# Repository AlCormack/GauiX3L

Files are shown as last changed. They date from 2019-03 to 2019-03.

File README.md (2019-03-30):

# Gaui X3L Speed
 
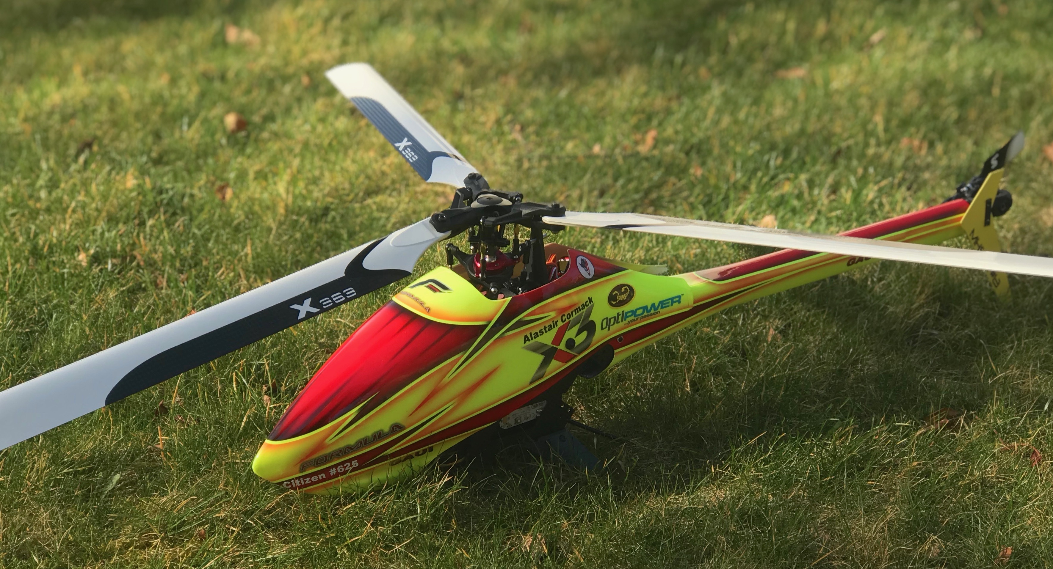
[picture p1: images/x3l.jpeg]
 <br />
 
A little video of it during a speed pass:<br />
 IMAGE ALT TEXT (http://www.youtube.com/watch?v=dyuTX_kXLzM "Gaui Speed X3L")
 
After getting my Gaui R5, I got the bug for speed. The R5 is a fantastic heli but I was looking for something even smaller for quick trips to the field. As it obviously had to be a Gaui heli the choice was simplified as the X3L had a fuselage and would support a motor that was much larger than a 325-380mm heli would normally use. The next decision was two or three blades. Never had a three blade heli and have fancied one but also liked the idea of greater stability on a small size heli. So got the: 

* Gaui X3L Basic Kit 3 blade - X3L Basic Kit

The tail is never highly loaded on a speed heli and the 3 blade tail setup would just cause more drag and therefore reduce the max speed. So ordered the required 2 blade tail parts:

* X3 Tail Pitch Slider Set
* X3 Tail Rotor Grip Assembly

For servos I wanted to run a high voltage setup. As I was in Taiwan the little Align servos looked good and had nice red fins to match the body colour (had to find some reason to justify them here):

* Align DS455M servo
* Align DS450M servo

For the motor there was only one choice. The monster Scorpion HK-3226, and to support the top of the motor shaft I added the: 

* Engine second bearing mount(for X3L)   

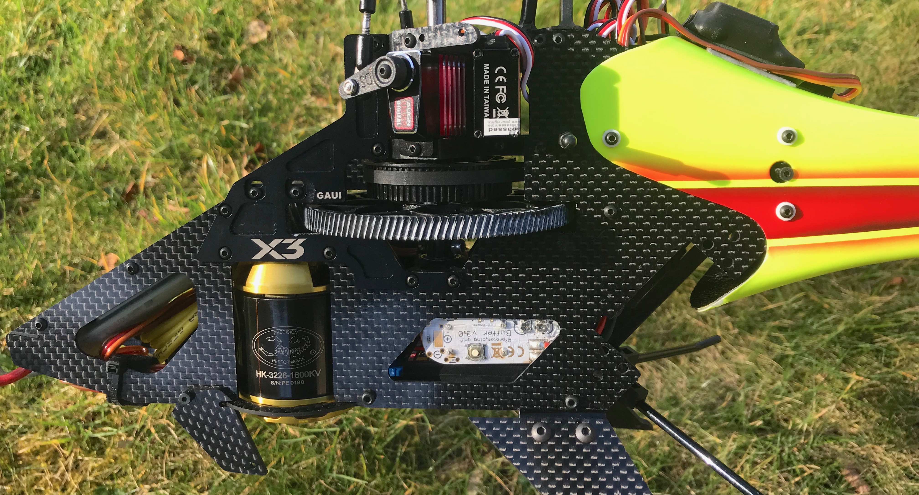
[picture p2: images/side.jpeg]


Also to support the blades I added the:

* X3 Main Blade Grips Parts Upgrade Pack (for 3 Blade)

For esc I tried the Hobbywing 50 but the telemetry setup is not great on it as it required a j-log to get the info I needed on PWM, and head speed. It also did not have a current sensor, so a MUI50 was needed too. A lot of extra electronics to fit in a small heli! YGE came out with their telemetry line. So I took out the Hobbywing (it has now gone in a standard X3 since) and put in a Yge 65lvt esc. This outputs directly to the Jeti RX and has a current sensor built in. Really nice esc, that also has an anti-spark setup. I use 5mm bullets as there is not much space for connector choice and this allows the positive to go one side and the negative the other of the frame. Since its launch Scorpion has now added an 80amp Tribunus, and I have had great success with the 200amp version on my R5 (destroyed 2 other brand esc's previously). If this was out at the time, I would have picked this as I am a huge fan of Georges, Tony and Scorpion as a whole, for all the fantastic support they provide in this hobby.

For main blades I have tried the Rail 326's but they did not max out the esc/motor even with a high pitch setup. I then tried the RotorTech 360mm 3 blade's. They were ok but I got a couple of very bad pitch ups and the heli was not stable at high speed. I then ordered two pairs of 363mm XBlades and used three of them. They turned out to really nice at high velocity, high RPM(3650) and high pitch angles (15 deg). For the tail blades I am using the Switch 60mm blades.

To get the head speed I wanted I needed a 14 tooth pinion, with a 5mm hole. Turned out this was not easy to find. Lynx had some end-of-line ones still in stock but they had the smaller 3mm hole. So ordered a bunch of them and got some 5mm drills and got my dad to use his lathe to drill out the centre. 

Getting the pitch of all three blades was not simple so ended up making my own turnbuckles. So ordered up some 3mmx25 titanium turnbuckles from a RC Car supplier. Drilled and Tapped Gaui ball ends to cope with 3mm thread (left and right threads). I use the Soko heli tool to get the setup all spot on (with the phone app to hand-hold me through all the setup steps. 

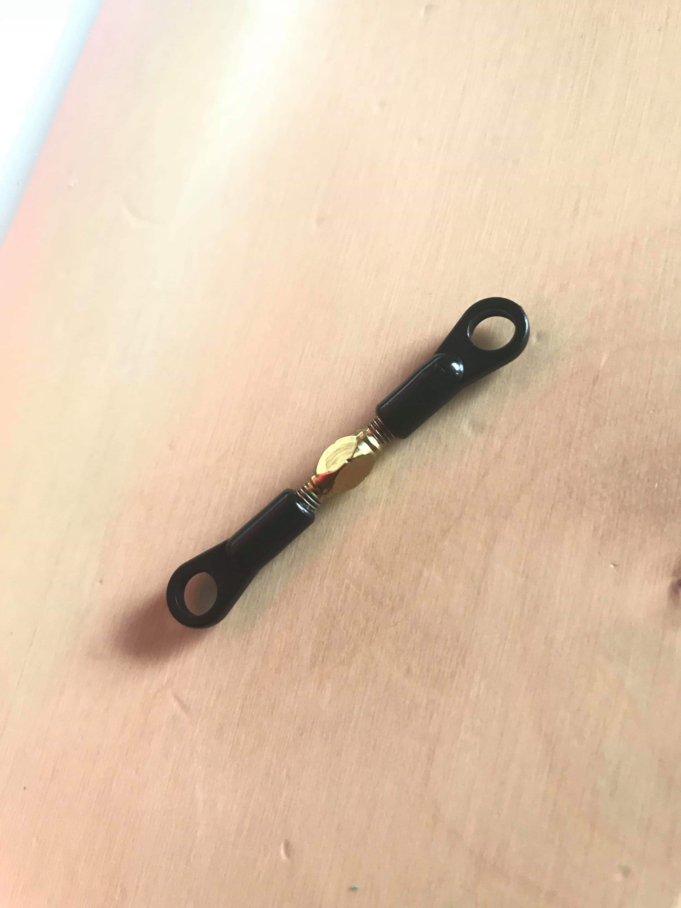
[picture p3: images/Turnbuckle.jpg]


Given the very high loads on the main gears I use Dryfluid Gear on both the gears and thrusts.

For flight packs I started with my favourite OptiPowers but getting stock of them is really tricky. I took a shot at the new Turnigy Graphenes:

* TURNIGY GRAPHENE 1500MAH 6S 65C LIPO

Amazingly they are incredible during a speed flight. Really shocked. The telemetry shows they keep their voltage even under huge load. One issue is that they are heavy but given how much power I have.. its not such a big deal.

For the flybarless the choice was simple: 
* BavarianDEMON 3SX with a Jeti Rex3 rx ([setup file](https://github.com/AlCormack/GauiX3L/blob/master/BD3SX/20190209%20Gaui%20X3L.hcx)) 

To measure the average speed I added my [speed GPS](https://github.com/AlCormack/SpeedGPS) and I use the [MHSFA speed application](https://github.com/AlCormack/JetiLua/tree/master/MHSFAApp) for the Jeti.

Given the high amp loads I have always had a worry about loosing power to the rx. So for safety I added a:
* R2 3x25 buffer.

The only problem that I have had so far is the radius arm breaking (on the three blade there is only one, unlike the two on the two blade). This had done over 100 flights. So now I am changing it every 50 flights (and the belt every 100.. make sure you use some silicon spray on the belt to help keep static down)<br />
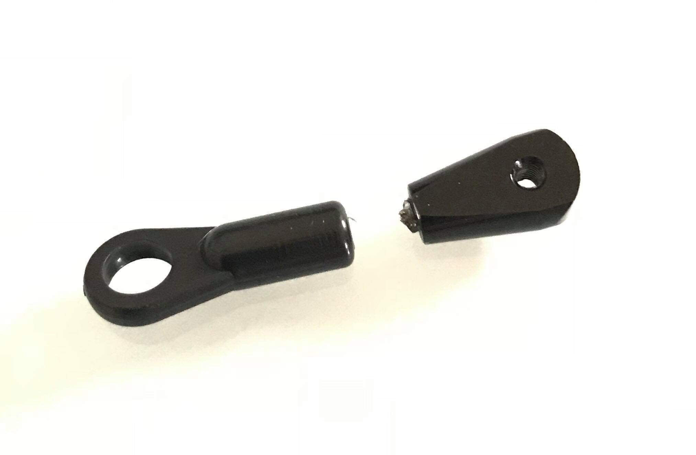
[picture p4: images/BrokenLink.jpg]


Now for some further slight optimisation. The tail was something that needed a bit of work. The gain I had to run to keep it all straight was more in the realms of a 3D setup (49 on the 3SX). Whereas on my R5 it was about 10 points less. The proper speed fuse helps on the R5 but also on my V1 the tail is adjustable, so like the big 700 speed machines you can build in some angle of attack on the rear fin. So out came the CAD software (Fusion 360 for me) and the 3D printer. I made a custom tail setup that has adjustable wedges to build in some tail wing angle. I have ended up using a 10degree wedge setup and have:
* lost about 10 points in the tail gain
* gained several kph in average pass speed
* gone to a smaller tail blade length

The final setup is pieced together as follows:<br />
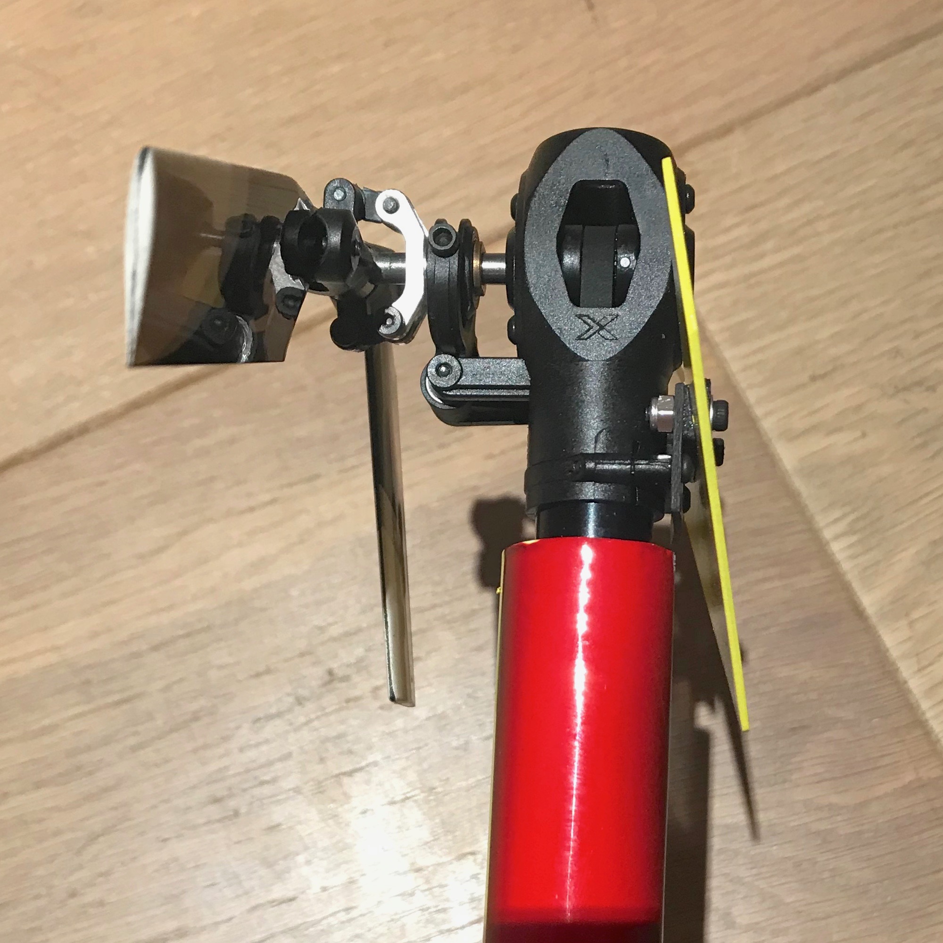
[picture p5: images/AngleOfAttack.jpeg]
<br />

I have provided a jig to enable to holes to be drilled in the correct locations (use double sided tape to hold the carbon sheet on while drilling). The jig also forms a good template for the adaptor to be cut out of 1mm carbon fibre sheet:<br />
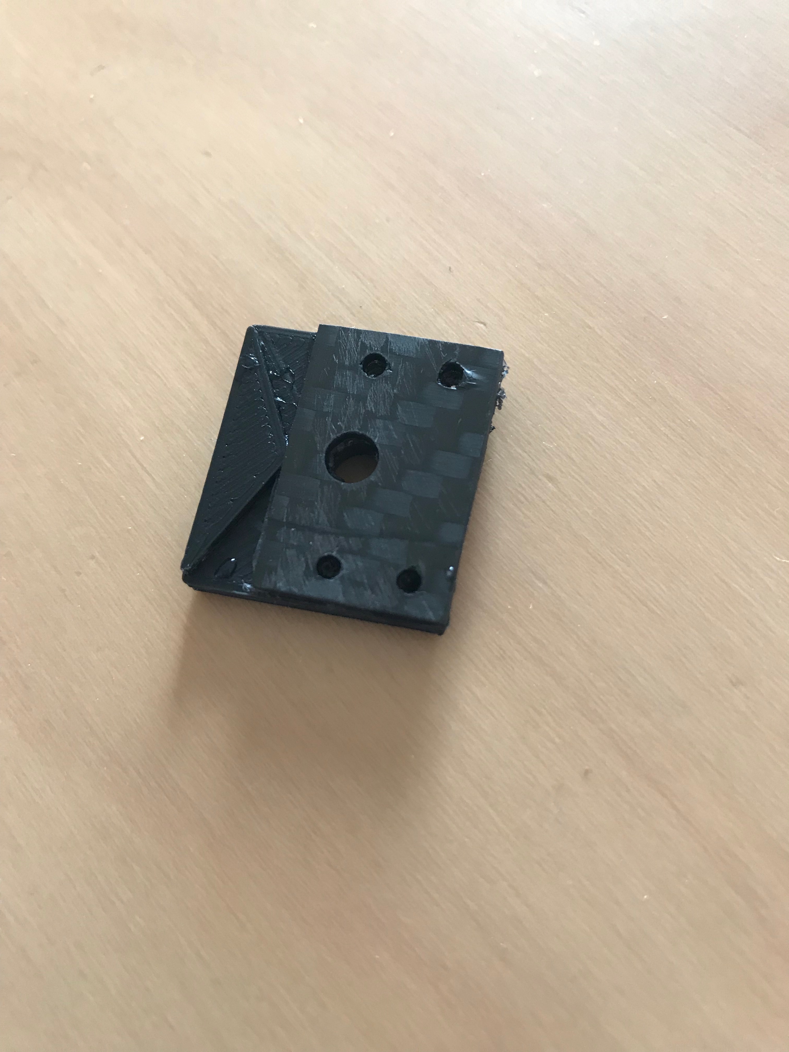
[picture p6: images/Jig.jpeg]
<br />
The adaptor is mounted as follows:<br />
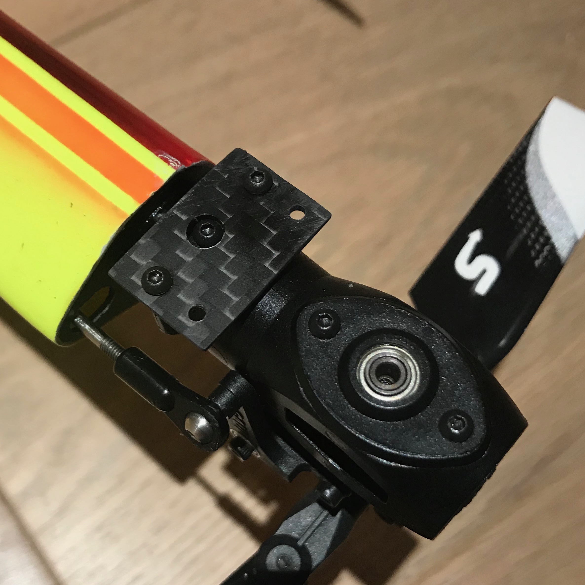
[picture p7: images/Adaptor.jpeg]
<br />

I have added all the files for this in this GitHub project for all of you to use. This includes [a pdf file](https://github.com/AlCormack/GauiX3L/blob/master/Fin%20Drawing%20v1.pdf) for the fin to be cut out of 1mm carbon fibre sheet. You can print this onto paper and cut it out to form a template or if you have a vinyl cutter I have added the [silhouette studio file](https://github.com/AlCormack/GauiX3L/blob/master/fin.studio3)  too.

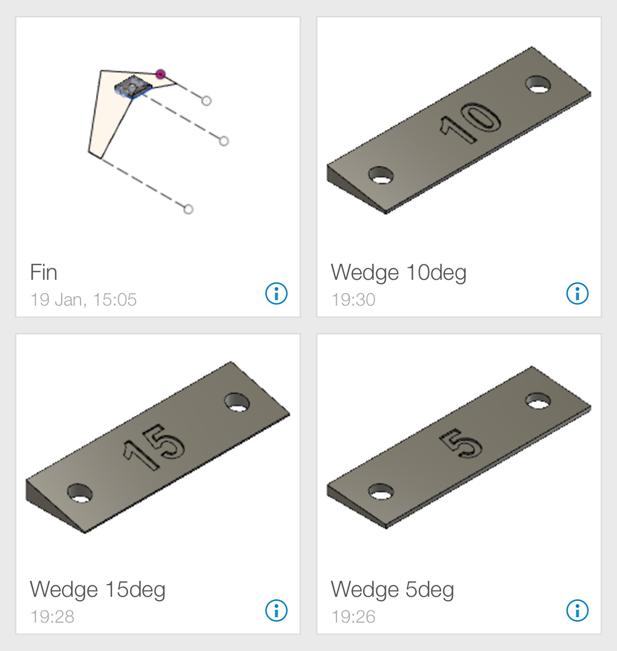
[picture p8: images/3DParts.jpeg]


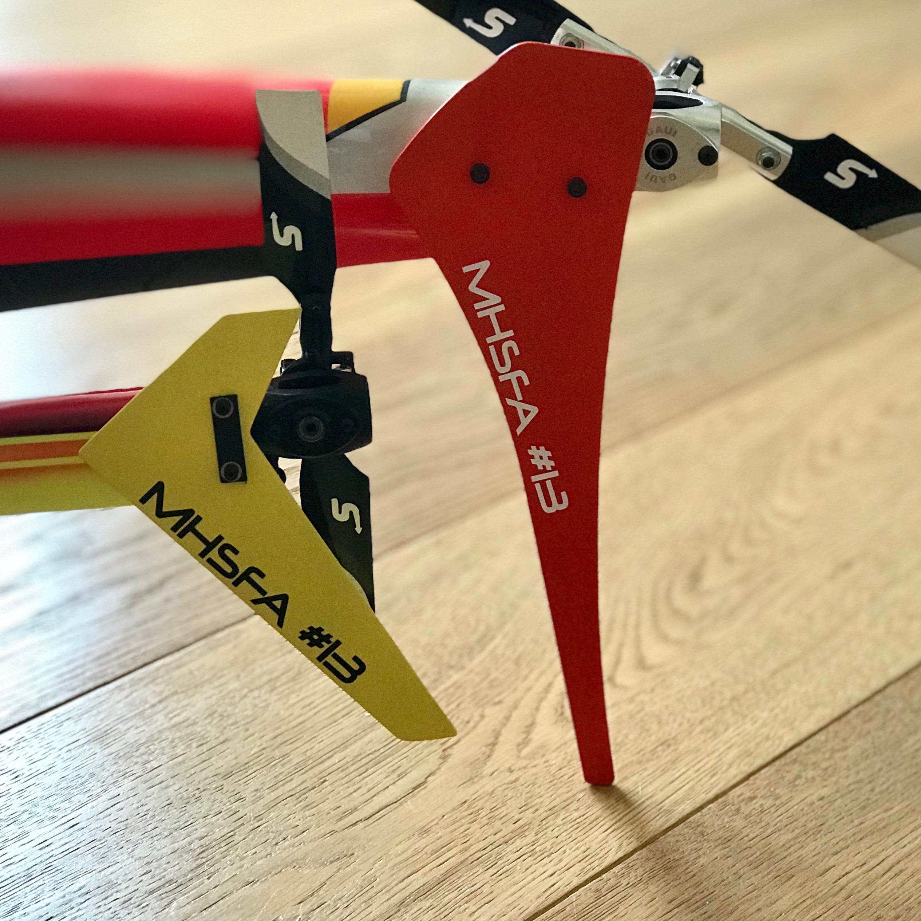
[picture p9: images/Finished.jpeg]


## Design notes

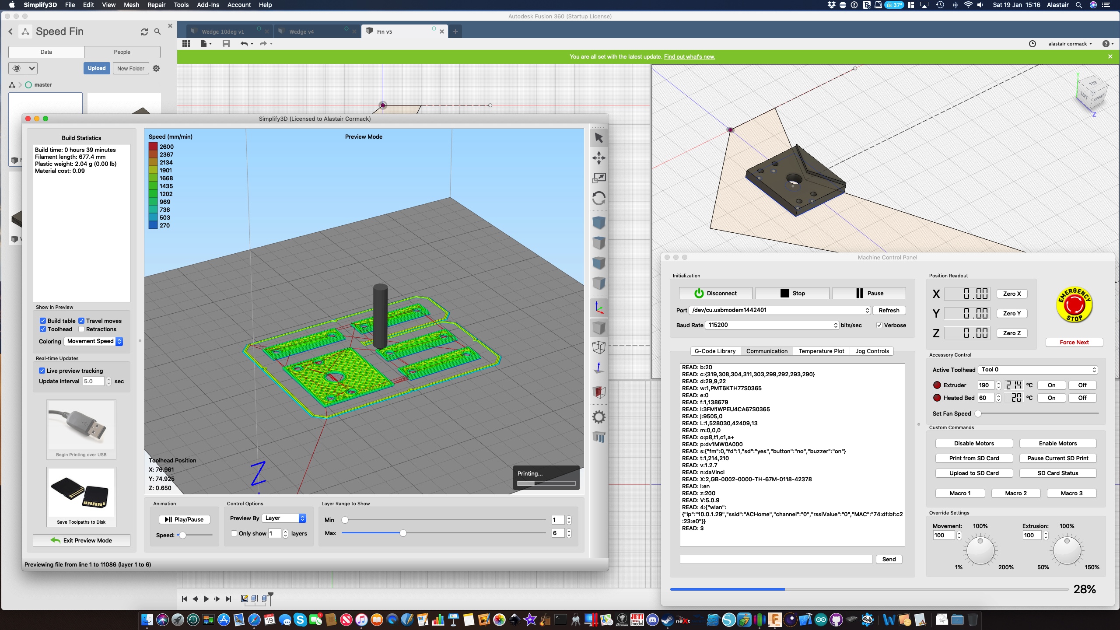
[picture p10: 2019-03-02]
images/3DPrintDialog.jpg

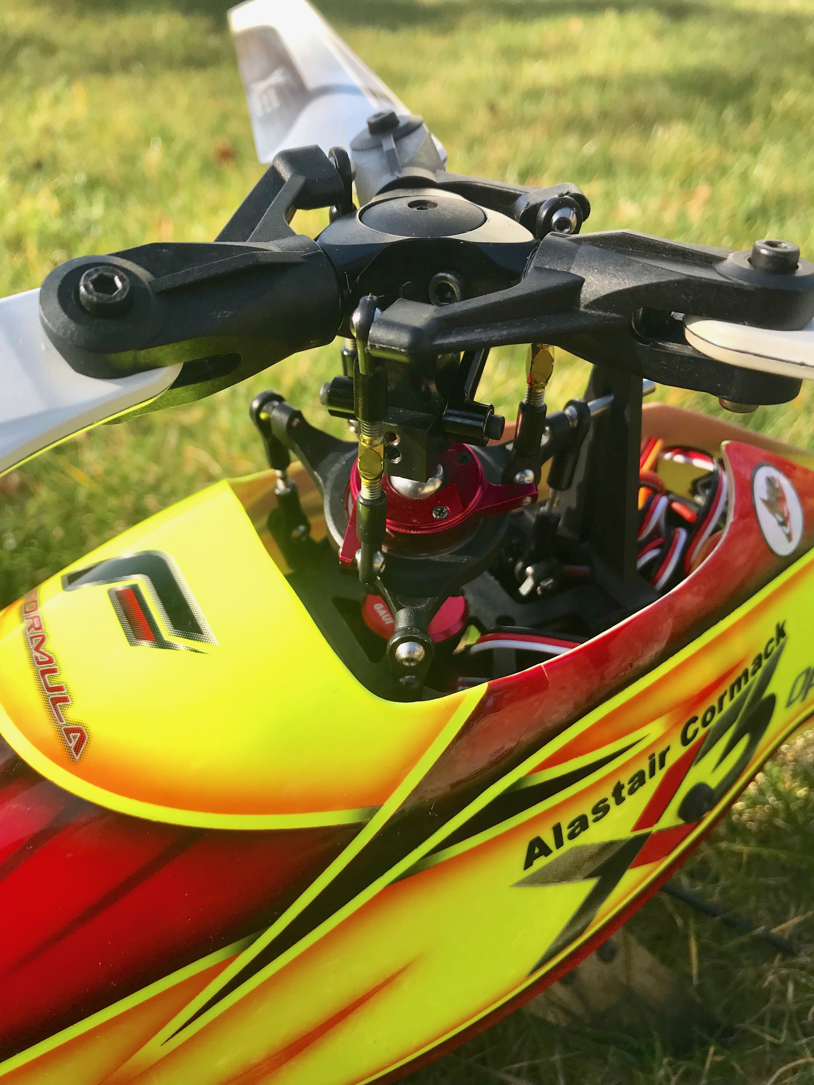
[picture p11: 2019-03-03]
images/head.jpeg

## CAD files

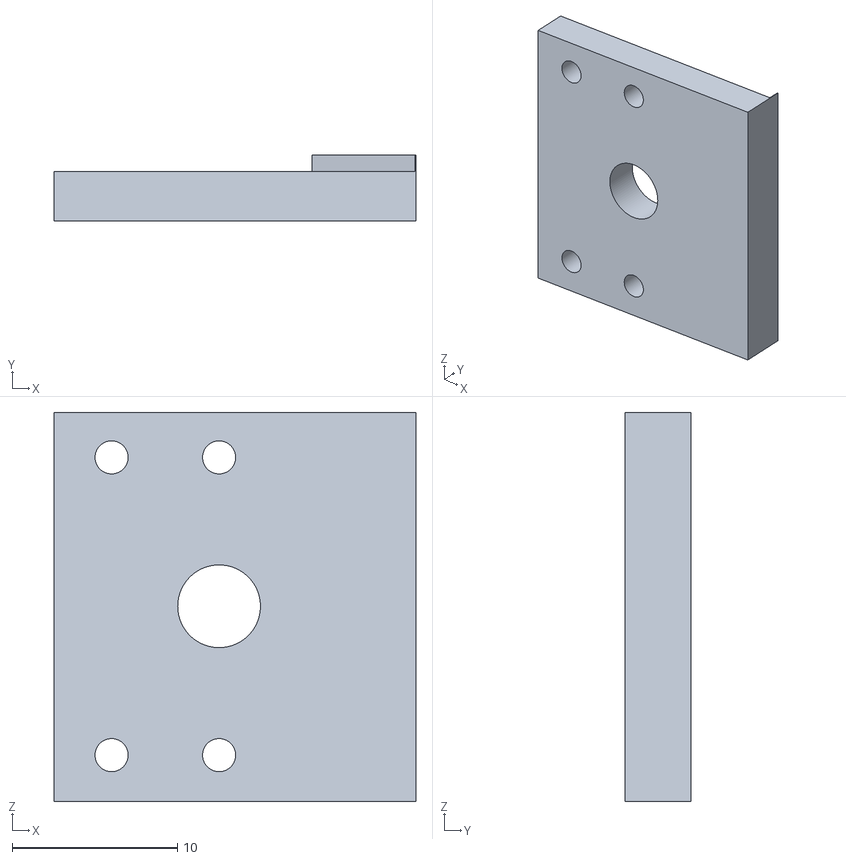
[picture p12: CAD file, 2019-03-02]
3dPrint/FinJig.stl
21.9 x 4.00 x 23.5

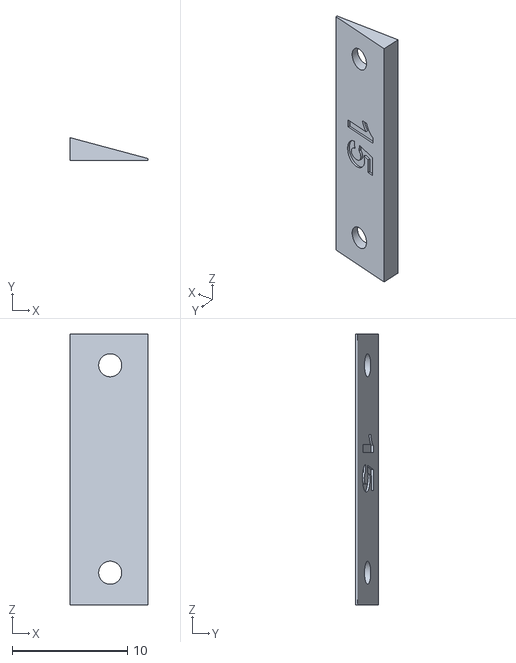
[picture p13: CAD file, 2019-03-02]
3dPrint/wedge-15deg.stl
6.75 x 1.97 x 23.5

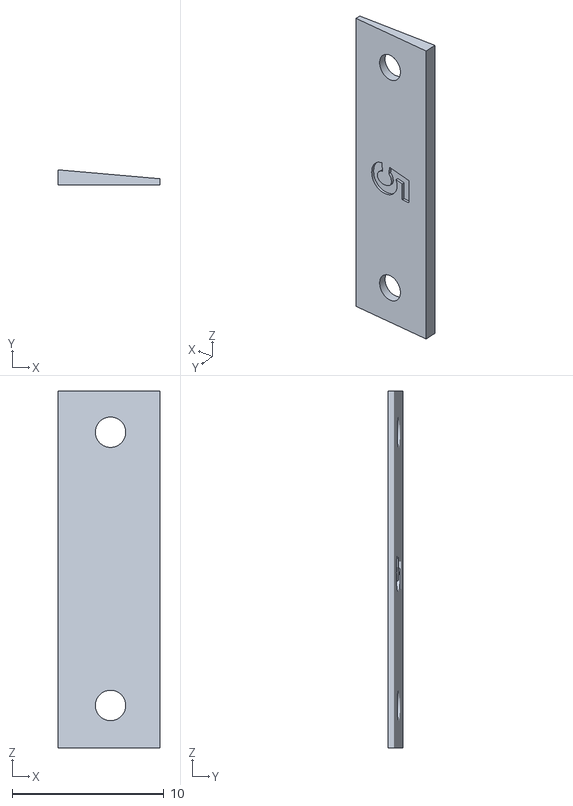
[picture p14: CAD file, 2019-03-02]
3dPrint/wedge-5deg.stl
6.75 x 1.02 x 23.5

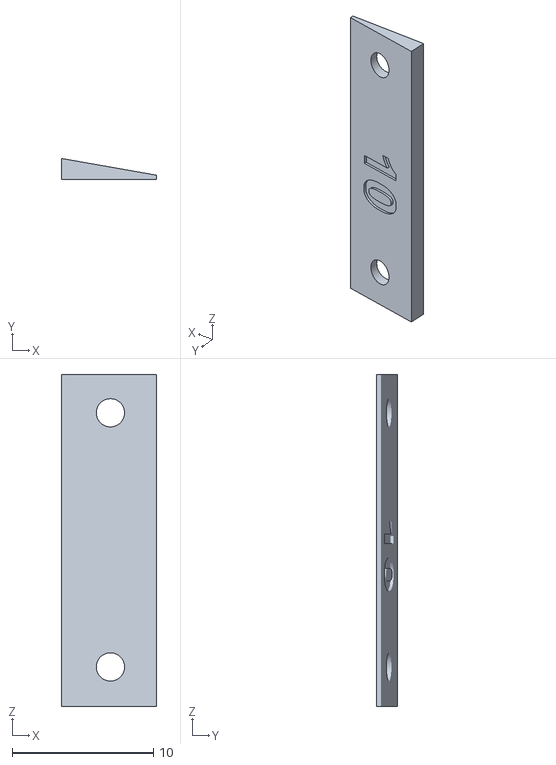
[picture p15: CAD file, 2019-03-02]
3dPrint/wedge-10deg.stl
6.75 x 1.50 x 23.5

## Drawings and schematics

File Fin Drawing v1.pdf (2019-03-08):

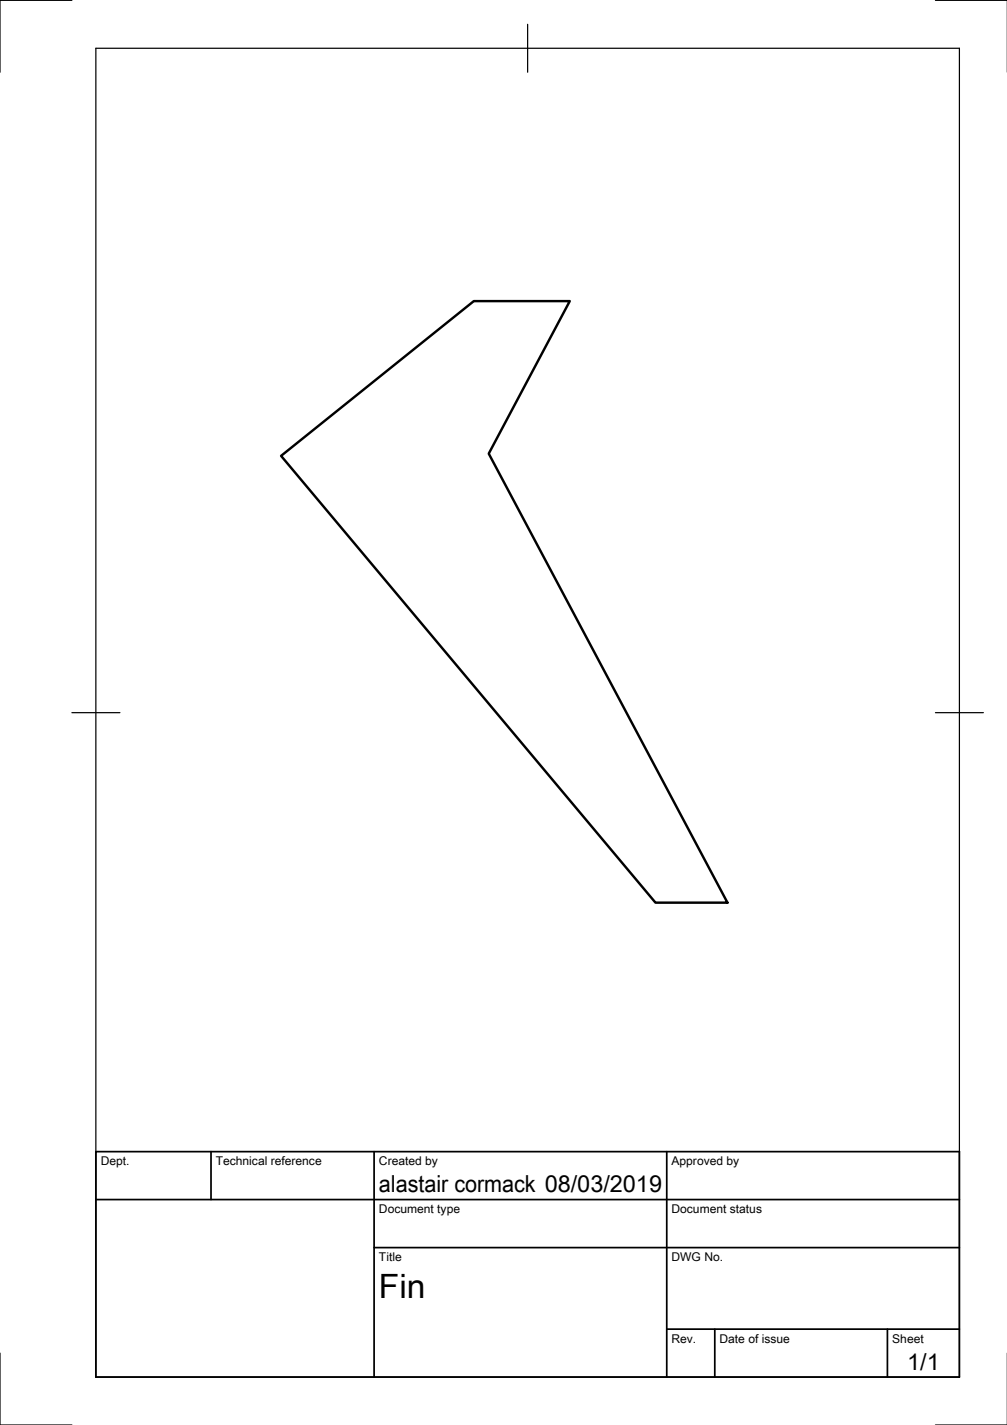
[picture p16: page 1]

Dept. | Technical reference | Created by alastair cormack 08/03/2019 | Approved by

Document type | Document status

Title Fin | DWG No.

Rev. | Date of issue | Sheet 1/1
